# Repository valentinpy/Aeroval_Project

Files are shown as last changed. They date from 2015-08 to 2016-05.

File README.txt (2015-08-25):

AEROVAL
Auteur: Valentin Py  - valentin.py@gmail.com
Date: 22.08.15

Ce projet est le développement d'un PCB ainsi que sa programmation.
Ce PCB est prévu pour le contrôle d'un quadri/octocoptère, mais est aussi utilisable pour un avion ou une voiture.
Pour plus de détails: voir le fichier "functionnalities.txt, ci-joint)

Matériel:
Un PCB de prototype a été développé et produit à 3 exemplaires. "Aeroval-v2-PCB1-proto1.pcbdoc" (gerber utilisés fournis)
Ce PCB fonctionne pour la plupart des fonctions prévues, mais il y aurait quelques améliorations /résolution de problèmes à effectuer:
	- connecteur micro-SD: à retourner de 180°, il n'est actuellement pas possible d'insérer une carte uSD.
	- transistors T1, T2, T3, T4: la numérotation du footprint est fausse, il faut corriger, sinon le transistor sera soudé "à l'envers"
	- Le solder mask est à modifier sous U4, afin de ne pas avoir de résine sous le pad thermique. (bien que ça fonctionne quand même dans l'état actuel)
	
La BOM est fournie et les supplier links sont remplis (pour la plupart) sur Altium.

Logiciel:
Le développement n'est pas terminé, il y a encore pas mal de travail à faire, mais les modules et les interfaces sont déjà programmés pour la plupart.

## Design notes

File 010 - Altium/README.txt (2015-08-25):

NE MARCHE PAS:
Positionnement uSD (retourner de 180°)
T1, T2, T3, T4: numéro des pins croisés (modifier footprint)
Pad thermique U4: enlever masque sous le step down (U4)

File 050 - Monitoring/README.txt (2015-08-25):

AEROVAL - Monitoring
Auteur: Valentin Py, avec une base de Lucas Wagner 
Date: 22.08.15

Télémétrie basique pour le projet Aéroval.
Programme non terminé, mais fonctionne déjà (du moins, en partie)

Fonctionnement: Brancher la carte Aeroval avec le cable USB sur l'ordinateur et choisir le port COM virtuel correspondant dans l'onglet connexion de ce VI.

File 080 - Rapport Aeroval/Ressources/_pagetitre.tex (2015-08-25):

\begin{titlepage}
%marge du haut et grande marge sur la page
%\headsep          = -10.mm
%\enlargethispage{5cm}

\begin{center} 
\hspace{12.45cm}
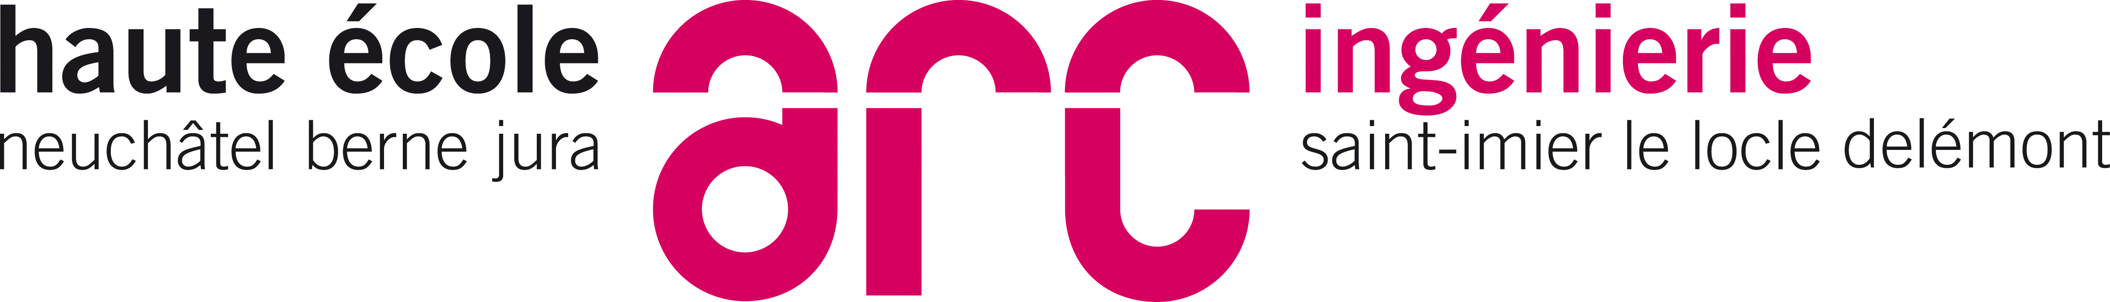
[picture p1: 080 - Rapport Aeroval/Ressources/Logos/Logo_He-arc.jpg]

\end{center}
\vspace{5cm}
% cette commande insert un espace de proportion 1 (par rapport au autre espace insert dans la mÍme apge)
% 1/3 espace, puis ligne
\noindent \rule{\linewidth}{1mm}
\begin{center}
\medskip
{\Huge \nomtitre}\\
\bigskip

\begin{minipage}{0.75 \textwidth}
\begin{center}
{\Large \sousTitre}\\
\end{center}
\end{minipage}~\\

\vspace{0.6cm}
\rule{1cm}{0.3mm}\\
\vspace{0.5cm}

\large \auteurs\\
\medskip
\dateCreation

% ligne, puis 1/3 espace
\noindent \rule{\linewidth}{1mm}
\vspace{3cm}

% Le complement d'information

%les logos des entreprises

\begin{center}

  \small \ecole \\
  %\small Ecole d'IngÈnieurs d'Yverdon-les-Bains \\
  \small \depart
  
\end{center}

\vspace{3.65cm}

%les noms (le "&" sÈpart les colonnes)
\small
{
\begin{tabular}{l@{: }l}
Dernière mise à jour &\today\\
\end{tabular} }

\end{center} 
\end{titlepage}

\newpage

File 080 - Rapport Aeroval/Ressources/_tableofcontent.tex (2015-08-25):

% table des matieres
\pagenumbering{Roman}	
\setcounter{page}{1} % on commence la numération a 1 sur cette page en notation romain
\setcounter{secnumdepth}{5}% profondeur de la table des matieres.
\setcounter{tocdepth}{2} 
\tableofcontents
\setlength{\parindent}{0 cm}% supprime les tabulations à chaque nouveau paragraphe
\newpage
\pagenumbering{arabic} % notation arabe

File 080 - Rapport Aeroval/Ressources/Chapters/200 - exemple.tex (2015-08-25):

% Chapter Template

\chapter{Nom du chaptitre} % Main chapter title

\label{Chapitre 2} % Change X to a consecutive number; for referencing this chapter elsewhere, use \ref{ChapterX}

\lhead{ \emph{Nom du chaptitre}} % Change X to a consecutive number; this is for the header on each page - perhaps a shortened title

Introduction chapitre

%----------------------------------------------------------------------------------------
%	SECTION 1
%----------------------------------------------------------------------------------------
\section{Nom de la section}

Texte section.
%-----------------------------------
%	SUBSECTION
%-----------------------------------
\subsection{Titre sous section}
Texte sous section
\begin{lstlisting}[frame=single,style=C]  % Start your code-block

int main()
{
	printf("exemple en C\n");
	return 0;
}
\end{lstlisting}

Exemple de texte.

\lstinputlisting[frame=single,style=C, title=main.c]{Ressources/Code_Source/main.c}
%\lstinputlisting[language=Python, firstline=37, lastline=45]{source_filename.py}

Texte
\rem{Ceci est une remarque}

\tmpnew{tmp new: A faire!}

\begin{lstlisting}[frame=single,style=Console]
$ Texte console
\end{lstlisting}
\pagebreak Apès un saut de page.

\begin{center} 
\hspace{12.45cm}
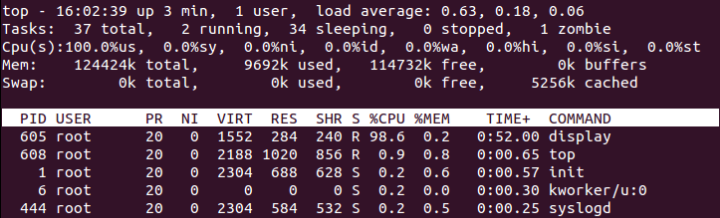
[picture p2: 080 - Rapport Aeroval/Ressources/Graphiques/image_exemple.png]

\end{center}
\vspace{1cm}

Texte

Liste
\begin{enumerate}
\item Premier
\item Deuxième
\item Dernier
\end{enumerate}

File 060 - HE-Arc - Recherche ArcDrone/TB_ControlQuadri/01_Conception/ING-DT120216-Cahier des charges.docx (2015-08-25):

Département de Génie Electrique Travail 12GEL-TB205

Travail de semestre et de Bachelor pour : Favre-Bulle Matthieu

## Système de contrôle de vol pour quadricoptère

### Introduction

La HE-Arc veut développer un quadricoptère comme démonstrateur de son savoir faire dans de nombreux domaines : construction légère en matériaux composite, électronique de contrôle embarquée, régulation automatique, traitement image, communication, gestion de l’énergie embarquée, génération de l’énergie embarquée etc…

### But du projet

Ce projet consiste à développer le système embarqué de contrôle de vol du quadricoptère. Ce système devra pouvoir s’interfacer soit sur les signaux en provenance d’un récepteur d’une télécommande du marché soit, à moyen terme d’un système de gestion de vol automatique embarqué via un bus à définir. Son rôle sera de maintenir le quadricoptère en vol stationaire et de lui faire faire les déplacements demandés par le système de commande supérieur : télécommande ou ultérieurement un système de gestion de vol embarqué. Il devra donc acquérir au moyen des différents capteurs les paramètres de vol du quadricoptère, afin d’être capable de donner des ordres de vitesse aux drivers des 4 moteurs brushless de l’appareil.

### Cahier des charges

Le projet consiste donc à :

1. Développer une carte électronique comportant un microcontrôleur ayant les fonctionnalités suivantes :
- Implémentation et acquisition d’un accéléromètre 3 axes (au centre de la carte)
- Implémentation et acquisition d’un gyroscope 3 axes (au centre de la carte)
- Implémentation et acquisition d’un magnétomètre 3 axes (au centre de la carte)
- Implémentation et acquisition d’un capteur de pression
- Interface de communication série vers capteur altimètre à ultrason, protocole à définir.
- Interface de commande de l’électronique des moteurs brushless à l’aide de signaux PWM normalisés dans le monde du modèle réduit.
- Interface avec un récepteur de télécommande du marché
- Prévoir une interface série dans le but d’implémenter un GPS
- Prévoir des connections pour une carte d’extension (Alim, signaux uP, …)
- Interface de communication radio bidirectionnelle (serial to RF), utiliser un module du marché, permettant d’implémenter des fonctions de télémétrie.
- Interface rapide avec une autre carte à processeur (gestion de vol automatique embarqué, interface et protocole à définir).
- Alimentation de la carte via la tension de sortie régulée d’un des contrôleurs brushless. Prévoir un régulateur de tension pour alimenter les composants de la carte.
- Mesure et surveillance de la tension et du courant de l’accu
- Dimensions de la carte : 100 x 100mm
2. Programmer cette carte pour permettre au quadricoptère d’obéir à des ordres en provenance de la télécommande en prenant en compte les mesures des capteurs et de le maintenir en vol stable. Les contraintes du logiciel sont :
- Prévoir une architecture logicielle en 3 couches étudiée durant les cours d’informatique embarquée
- Prévoir un monitoring permettant d’envoyer et recevoir différents paramètres toutes les 20msec via l’interface RF : La trame utilisée pour la communication devra permettre d’ajouter facilement le monitoring d’autres variables et également la réception de valeurs de variables en provenance du sol.
  - 3 axes accélérations
  - 3 axes vitesse angulaire
  - 3 axes magnétomètre
  - Altitude
  - Tension accu
  - Courant de l’accu
  - Valeur PWM envoyées à chaque moteur

Projet microtechnique

Un autre travail de bachelor dans le domaine des microtechniques sera en charge de la conception du quadricoptère. Communiquer avec l’étudiant responsable de ce projet, afin de vous synchroniser sur l’implantation de la carte électronique, la connectique, etc.

Résultat du projet

A la fin du projet, on disposera :

* d’une liste complète décrivant les solutions étudiées
* d’une présentation détaillée de la solution retenue
* de deux cartes électroniques montées et testées
* d’une architecture logicielle (modèle 3 couches) détaillée
* du code source implémenté sur le dispositif
* d’un schéma détaillé avec liste de pièces et prix du dispositif
* d’une documentation détaillée décrivant l’ensemble du dispositif
* d’un mode d’emploi simplifié

Guide du projet

Phase 1 Conception, calculs et études des solutions (capteurs, choix du microcontrôleur, …)

Phase 2 Présentation de la solution envisagée aux responsables du projet (GHU, PAD, MHU, YME)

Phase 3 Développement matériel, recherche des composants, édition du schéma (Altium Designer)

Phase 4 Réalisation du layout de la carte (Altium Designer)

Phase 5 Sous-traitance de la production des circuits imprimés, et commande des composants

Phase 6 Développement du logiciel du microcontrôleur

Phase 6 Montage du premier prototype, programmation, éventuellement dépannage

Phase 7 Mise en service et tests

Phase 8 Correction de problèmes éventuels (mise à jours schéma et layout)

Phase 9 Documentation

Phase 10 Montage de la 2ème carte électronique (éventuellement production d’un nouveau circuit)

N.B : Prendre garde aux délais de livraison des composants, en principe il faut toujours utiliser des composants de stock chez les distributeurs (Digikey, Mouser, Farnell, Distrelec,...).

# Rapport et évaluation

Le travail de diplôme a entre autre pour but d’évaluer les facultés de l’étudiant à aborder, conduire, exécuter et documenter un travail industriel complet. Spécifié par un cahier de charges et décrit dans un mémoire, il est souvent pluridisciplinaire. Les étudiants voudront bien dans les 4 premières semaines du travail, estimer et planifier les tâches à accomplir.

Délais et rapport selon directives ci-jointes.

HE-Arc/YME/février 2012

ING-DT120216-Cahier des charges2/3 YME-dernière mise à jour : 16.02.2012

ING-DT120216-Cahier des charges1/3 YME-dernière mise à jour : 16.02.2012

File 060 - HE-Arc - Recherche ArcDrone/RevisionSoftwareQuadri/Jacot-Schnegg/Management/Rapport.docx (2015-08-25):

Arc-Drone

Description de la solution retenue

Guillaume Jacot & Alexandre Schnegg

26/01/2013

# Introduction

Le présent document a pour but de résumer le travail effectué sur le quadricoptère afin que le prochain intervenant sache ce qui a été fait. On y trouve les explications concernant la correction des bugs des interfaces ainsi que le fonctionnement du monitoring, de l'acquisition de l'orientation et de la régulation du quadricoptère.

# Résumé du débug des interfaces

## I2C

On a codé une nouvelle fonction permettant la lecture de plusieurs bytes d’un coup. On l’a utilisée pour lire la valeur de tous les axes de l’accéléromètre d’un coup. La lecture multiple ne fonctionne pas avec le gyroscope donc on a laissé comme c’était fait.

On a préféré tester si le bus était libre plutôt que de faire une attente active dans tous les cas.

On a corrigé la fonction d’envoi par I2C. Quand on envoie l’adresse du périphérique souhaité sur le bus I2C, on met le dernier bit à 1 ou à 0 en fonction de si on veut lire ou écrire un registre. Dans notre cas, le dernier bit de la donnée était aussi modifié donc la configuration des périphériques I2C (par exemple la vitesse d’acquisition des données) n’était pas celle que nous voulions.

## Magnétomètre

Une fois qu’une valeur avait été lue, toutes les lectures suivantes nous donnaient les mêmes résultats. On a découvert ceci en faisant des tests avec un aimant :

- Si l’aimant était mis avant le démarrage du programme, les valeurs mesurées étaient grandes et ne bougeaient pas quand on retirait l’aimant.
- Si l’aimant n’était pas mis avant le démarrage du programme, les valeurs mesurées étaient beaucoup plus petites, mais ne bougeaient pas quand on mettait l’aimant.

Ceci était dû au bit LOCK du magnétomètre qui se met à ‘1’ quand on lit la 1re valeur et qui empêche donc l’actualisation des mesures. Celui-ci ne se remettait malheureusement jamais à ‘0’ ce qui empêchait la modification des valeurs.

Pour remédier à ce problème, on a également utilisé notre fonction de lecture multiple par I2C pour lire tous les axes d’un coup. Le magnétomètre remet automatiquement le bit LOCK à ‘0’ quand on a lu toutes les valeurs. Des fois, celui-ci ne se remet pas à ‘0’ automatiquement, on renvoie donc le mode d’acquisition (single ou continuous) au magnétomètre pour forcer sa remise à ‘0’.

On a également modifié le gain, car il était au minimum et le champ magnétique terrestre est très faible (environ 0.5 gauss).

## PWM

La largeur des impulsions variait périodiquement. On a mis pas mal de temps à détecter que ceci venait d’une simple erreur de soustraction dans l’interface du timer. A chaque détection de flanc du signal d’entrée, on sauvegarde la valeur du timer. Ensuite, on calcul la différence entre les 2 mesures. Lorsque le 2e flanc (flanc descendant) est détecté après que le timer soit revenu à 0, il faut prendre la valeur maximale du timer moins la différence entre les 2 valeurs mesurées pour avoir un résultat correct. Le code avait été fait pour une valeur maximale du timer de 65535 pourtant le timer est configuré pour compter de 0 à 62’500 seulement donc les mesures étaient faussées.

Une fois ce problème corrigé, on pouvait encore observer des petites variations dans la mesure du duty cycle alors que le signal d’entrée ne variait pas. Ceci était dû à la façon de sauvegarder la valeur du timer à chaque flanc. En effet, on sauve les valeurs dans des variables globales qui sont ensuite lues par une autre fonction (celle qui fait la soustraction entre les deux valeurs).

Lorsqu’une nouvelle impulsion arrivait (détection du flanc montant), on sauvait la première valeur du timer. Le problème se posait dans le cas où l’autre fonction venait lire, avant le flanc descendant, les deux variables. On avait donc la valeur du timer au flanc descendant de l’ancienne impulsion et au flanc montant de la nouvelle impulsion, ce qui nous donne un résultat faussé.

Pour remédier à ce problème, on met la première valeur dans une variable temporaire et à la fin de l’impulsion, on sauve les deux valeurs dans les variables globales (les deux changent donc en même temps et on a toujours les deux valeurs se rapportant à la même impulsion).

Quand on lit un signal venant de la télécommande, celui-ci a une période de 20 ms, mais l’impulsion ne dure qu’entre 1 et 2ms. Ceci nous donne donc un duty cycle entre 0.05 (5%) et 0.1 (10%). La précision des float n’étant pas très bonne, on a préféré travailler directement avec la valeur en UInt16 (qui représente la soustraction des 2 valeurs du timer). On convertit ensuite cette valeur dans une plage allant de 0 (0%) à 1 (100%).

## Attentes actives

Nous avons remplacé toutes les attentes actives par des machines d’états pour gagner en rapidité car rien que le capteur de pression prenait environ 70ms avant de renvoyer une valeur par exemple.

# Monitoring

## Envoi des données

Les données sont envoyées à l'application labview par le bai d'une communication série sans fil sous forme de chaînes de caractères.

La trame a le format suivant:

1. Start
2. Capteur
3. Type de donnée (entier ou flottant)
4. Données
5. Stop

Lorsque le capteur nécessite l'envoi de plusieurs valeurs (par ex: 3 axes pour l'accéléromètre), les données valeurs sont séparées par le caractère '|'.

La génération des trames se fait avec le l'utilitaire generateTrame.h.

## Application labview

### Fonctions

Voici une liste des capteurs dont les valeurs peuvent être lues par l’application Labview :

- Accéléromètre (3 axes)
- Gyroscope (3 axes)
- Magnétomètre (3 axes)
- Pression
- Température
- Altitude (pas encore fonctionnel)
- Tension de la batterie
- Courant consommé
- Orientation du quadricoptère (3 axes, valeurs après filtrage)
- Signaux PWM (commande des 4 moteurs)

Voici à quoi ressemble l’application :

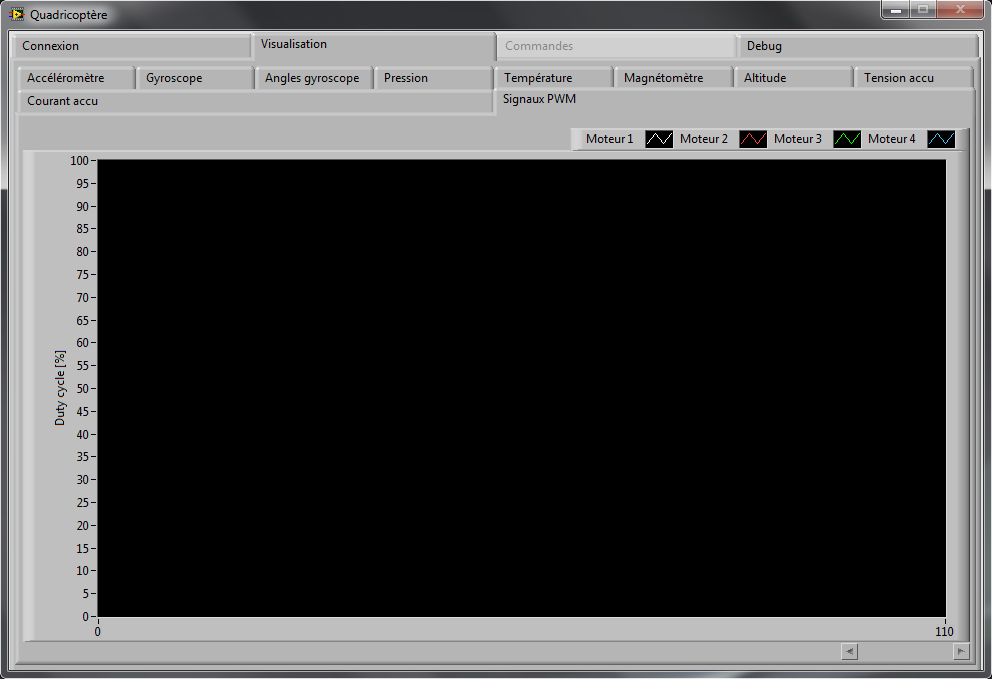
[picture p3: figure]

Fonctions des 4 onglets principaux :

- Connexion : permet de sélectionner sur quel port COM est connecté le récepteur RF, de s’y connecter/déconnecter et de quitter l’application.
- Visualisation : permets de visualiser un graphique par capteur (chaque capteur est sur un onglet séparé) représentant l’évolution des mesures de celui-ci (plusieurs courbes sur le même graphique pour les capteurs avec plusieurs axes ou pour les signaux PWM des 4 moteurs).
- Commandes : permets d’envoyer des commandes au quadricoptère. Cet onglet n’est pas encore fonctionnel.
- Débug : permets de visualiser tout ce qui a été reçu par RS232 et détecter d’éventuelle erreur dans les valeurs envoyées par le quadricoptère. On y voit également la dernière commande reçue ainsi que l’état de l’application.

### Fonctionnement

L’application est basée sur une machine d’état. On passe d’abord par un état d’initialisation, puis par la connexion au RS232 et enfin on va lire les données reçues en boucle. Un état est aussi prévu pour la déconnexion du RS232.

Chaque fois qu’une trame est reçue, l’application va la placer dans une file d’attente. C’est une deuxième boucle qui tourne en parallèle qui va récupérer cette trame, la décoder et ajouter les valeurs qu’elle contient sur le bon graphique.

A chaque fois que la machine d’état passe à l’état « Init », « Connect » ou « Disconnect », une notification est envoyée à une troisième boucle qui tourne en parallèle. Celle-ci s’occupe d’effacer les graphiques et d’activer/désactiver certaines fonctions selon l’état de l’application.

# Acquisition de l'orientation

## Systèmes d'axes des capteurs

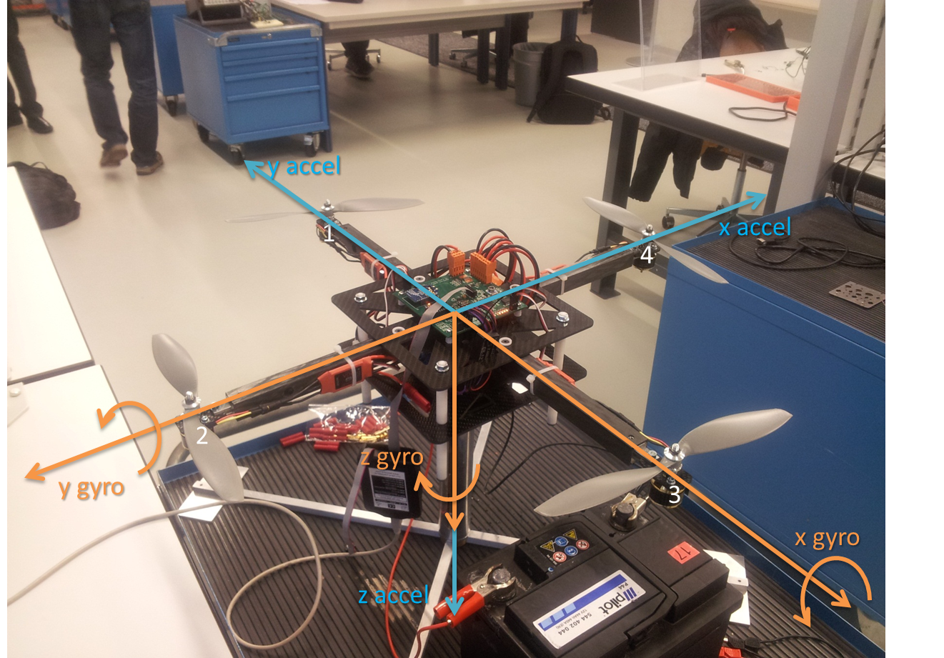
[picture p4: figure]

## Algorithme d'acquisition de l'orientation

Premièrement, les données brutes des capteurs sont transformées en grandeurs physiques (g pour l'accélération et deg/s pour le gyroscope. La dérive du gyroscope est compensée à ce moment-là.

Le vecteur d'accélération est ensuite transformé en angles dans le référentiel du gyroscope. La valeur de ces angles est convertie en degrés.

Dès lors, les valeurs sont filtrées par un filtre du premier ou du second ordre, à choix. Les paramètres du filtre sont réglés dans les définitions du fichier mOrientationProcessing.h. On peut régler la fréquence d'échantillonnage (kDt), le Tau du filtre (kTau) et les coefficients du filtre (kA et kB, respectivement pour le passe-haut (gyroscope) et le passe-bas (accéléromètre)).

# Régulation

Tous les paramètres de la régulation sont réglables dans mRegulation.h.

La régulation fonctionne sur le principe suivant : une puissance constante est appliquée à tous les moteurs. La régulation va calculer la puissance à rajouter ou à enlever. L’erreur est calculée sur les angles xz et yz, qui correspondent aux deux axes d'inclinaison possible; la régulation est calculée pour ces deux angles. La puissance à appliquer au moteur qui sont sur un axe est calculée comme ceci: pour le premier on additionne la puissance calculée par la régulation à l'offset, pour l'autre on la soustrait.

Chaque régulateur (P et I) est implémenté séparément dans une fonction.

Il est nécessaire de régler l'angle maximum que peuvent avoir les angles d'orientation. Lorsque le quadricoptère et sur le support il ne peut s'incliner que de 20°.

# Gestionnaires

La régulation devant être exécutée à un temps régulier précis, le code doit être exécuté dans une interruption. Pour se faire, nous avons créé trois fonctions execute spéciale, gInput_ExecuteInt, gCompute_ExecuteInt, gOutput_ExecuteInt destinées à être appelée dans l'interruption iPit_INTPit1. Les autres fonctions execute sont appelées dans la boucle principale du main.

# Démarrage du quadricoptère

Quand on branche l’alimentation, les drivers moteurs se configurent en fonction du signal PWM qu’ils reçoivent. Ils considèrent que celui-ci représente 0%. Ceci permet d’utiliser correctement toute la plage de puissances. On doit donc envoyer un signal PWM constant représentant le 0% au démarrage du programme avant de pouvoir faire tourner les moteurs à la vitesse souhaitée.

Par mesure de sécurité, le quadricoptère ne démarre pas tout de suite lorsque le programme est démarré. Il faut maintenir les joysticks de la télécommande en position 0 (en bas à gauche) pour que les moteurs démarrent. Sitôt qu’un joystick est relâché, les moteurs s'arrêtent.

# Leds témoin

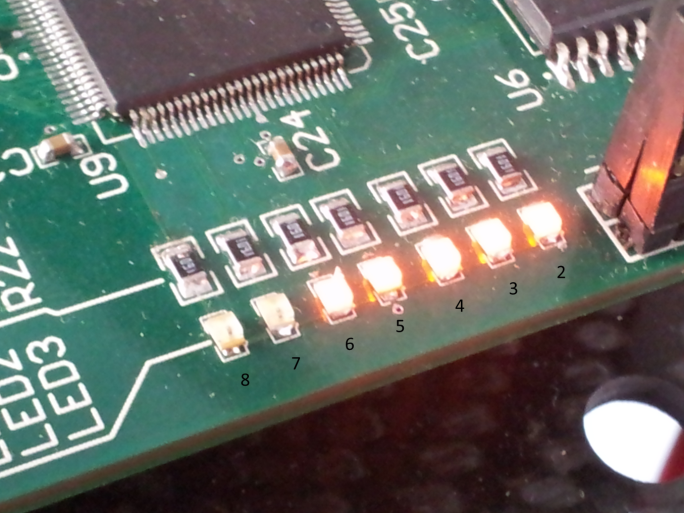
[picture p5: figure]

2. Allumée après le setup des modules
3. Allumée après l'open des modules
4. Allumée après le setup des gestionnaires
5. Clignote à chaque cycle du main
6. Clignote à chaque appel de l'interruption iPit_INTPit1
7. Témoin d'activation des moteurs

Résumé du travail effectué sur le quadricoptère 6/6

Guillaume Jacot INF3iie 28 janvier 2013 Alexandre Schnegg

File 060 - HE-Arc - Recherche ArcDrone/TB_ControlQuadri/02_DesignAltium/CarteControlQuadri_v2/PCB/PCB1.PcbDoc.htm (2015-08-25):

Reporting Options

# File in Previous Format

Date | : | 04.08.2015
Time | : | 11:08:36
Filename | : | C:\Users\valentin.py\Documents\Aeroval\PyValentin\TB_ControlQuadri\02_DesignAltium\CarteControlQuadri_v2\PCB\PCB1.PcbDoc

Version | Warning
Altium Designer update 19 | CAUTION - Air Gap Width attribute was introduced to Polygon Connect Style Rule. Air Gap Width attribute now controls the distance between poured polygon and pads on the same net - this value was previosuly taken from clearance rule while ignoring net subscope leading to sometime unexpected results.
Release 13 | CAUTION - Silkscreen Over Component Pads Rules are converted to Silk To Solder Mask Clearance Rules. Suggest examining rule scopes for accuracy.
Release 14 | CAUTION - The Differential Pairs Routing rule added support for control of the width. Be aware that Width rules pertaining to differential pairs need to be manually moved to the Differential Pairs Routing rule.

This file was generated by an earlier version of the software

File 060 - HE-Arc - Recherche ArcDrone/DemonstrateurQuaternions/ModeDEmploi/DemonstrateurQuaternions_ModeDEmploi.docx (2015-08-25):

# Mode d’emploi démonstrateur quaternions

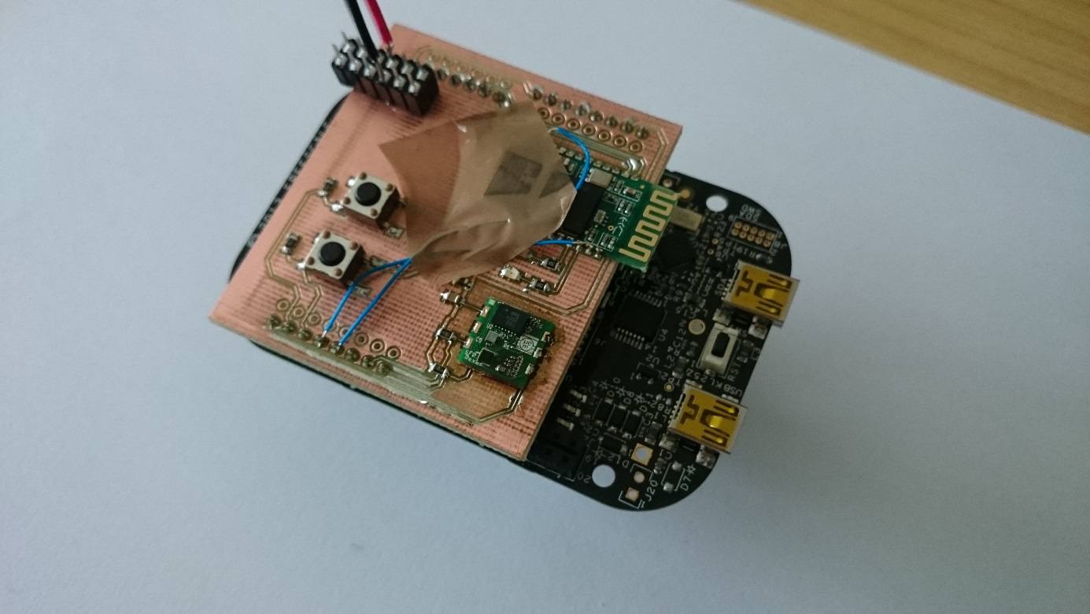
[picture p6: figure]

# Introduction

Le démonstrateur quaternions est une plateforme hardware qui a pour but de lire les valeurs d’un capteur de fusion 9 axes pour ensuite les récupérer avec un ordinateur.

La plateforme utilise un kit de développement de chez freescale, la FRDM-KL25Z. Une carte d’adaptation a été réalisée, elle comporte deux boutons poussoirs, le capteur de fusion ainsi qu’un module bluetooth. Cette carte d’adaptation est branchée sur le kit freescale.

Ultimement, les données seront utilisées pour évaluer les performances de l’algorithme de Madgwick.

# Implentation

Sur l’image ci-dessous, nous pouvons voir :

- Le bluetooth et son antenne (HC-05)
- Le capteur de fusion (EM7180)
- Les boutons poussoirs
- La carte de développement freescale (FRDM- KL25Z)

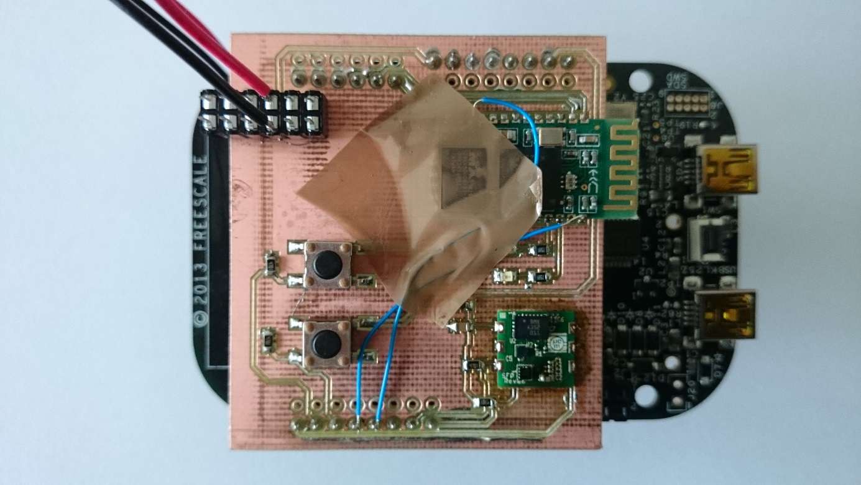
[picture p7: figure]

Ci-dessous, nous voyons :

- La pile d’alimentation 9V
- La fixation de la pile avec des velcros

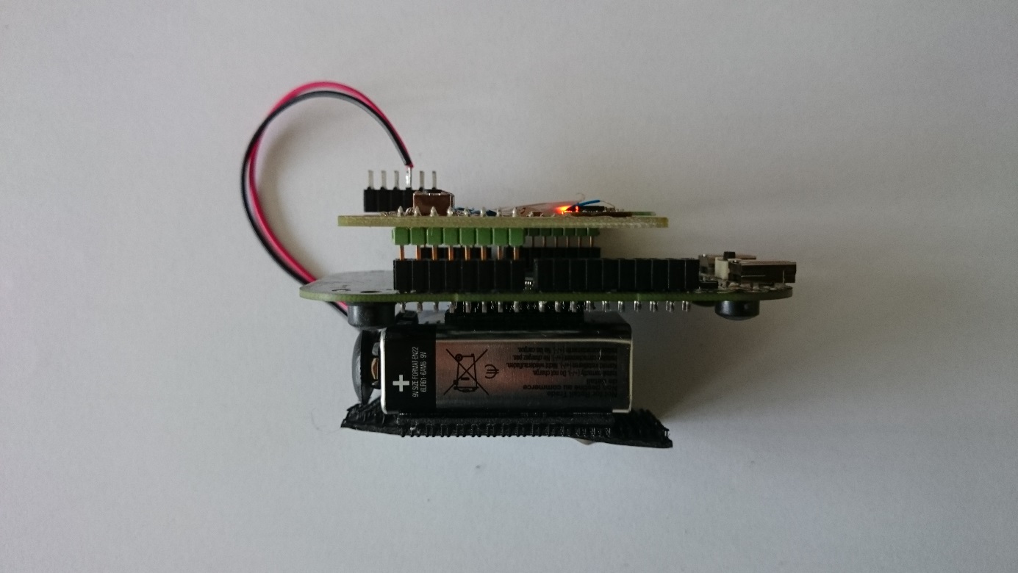
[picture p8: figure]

# Datasets

Des datasets ont été faits.

La fréquence de la mesure est de 100Hz.

Pour ce faire, nous avons fixé le démonstrateur sur une chaussure. Un velcro est passé entre les lacets.

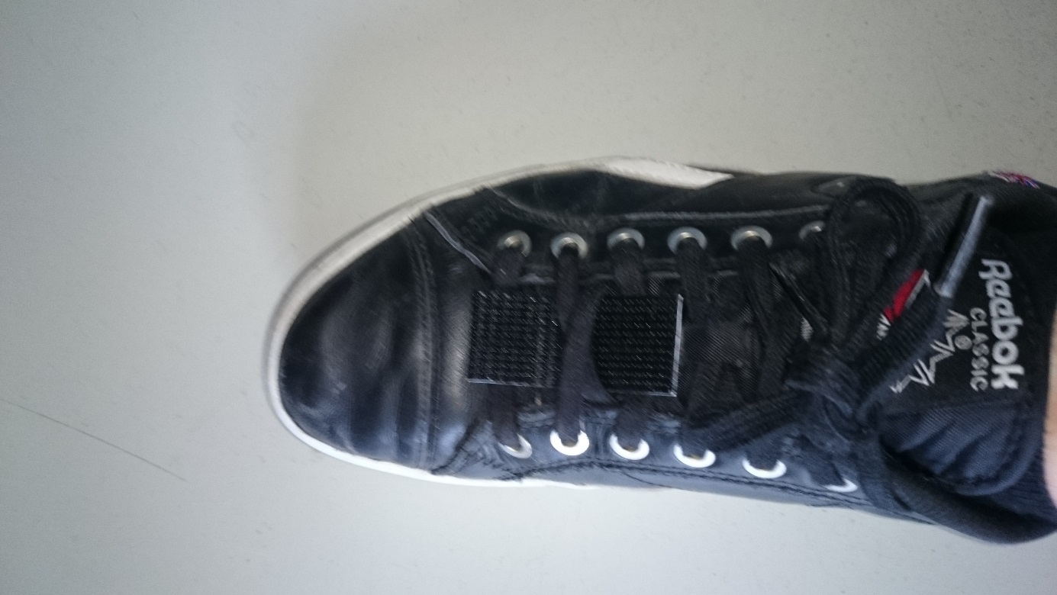
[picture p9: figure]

Des élastiques sont utilisés pour stabiliser la plateforme le plus possible et ainsi éviter le bruit durant la mesure.

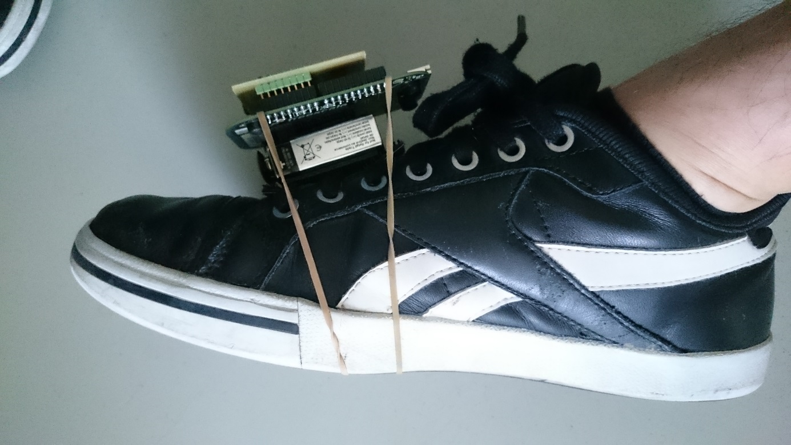
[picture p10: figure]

# Connexion du bluetooth et récupération des données

Les données du capteur de fusion sont transférer vers un ordinateur grâce à un module bluetooth. Elles sont ensuite récupérées dans un terminal (TeraTerm).

Les caractéristiques de transmission sont les suivantes :

- Baudrate : 460900
- Stop bit : 1
- Parity : none

Pour réaliser le transfert de données, il faut :

1) Mettre en marche le bluetooth de l’ordinateur
2) Connecter le module bluetooth HC-05 (password : 1234)
3) Ouvrir les paramètres du bluetooth de l’ordinateur et créer un portcom
4) Ouvrir un terminal et se connecter sur le portcom correspondant avec les bons réglages de communication

Quand la connexion n’est pas effectuée, la led TODO de la carte clignotte vide.

Lorsque la connexion est établie, la led TODO est allumée et la led TODO clignotte deux fois toute les secondes. Attention, si Teraterm n’a pas ouvert de connexions sur le portcom, les leds ne passent pas en état connecté…

# Enclencher et déclencher la mesure

Le bouton poussoir TODO permet d’enclencher et de déclencher l’envoi de données via bluetooth.

Une led bleue sur le kit de développement FRDM- KL25Z s’allume lorsque les données sont en train d’être envoyées.

# Conclusion

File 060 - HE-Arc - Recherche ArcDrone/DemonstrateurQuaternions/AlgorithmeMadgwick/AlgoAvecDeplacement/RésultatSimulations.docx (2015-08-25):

Ligne droite, seulement gyroscope

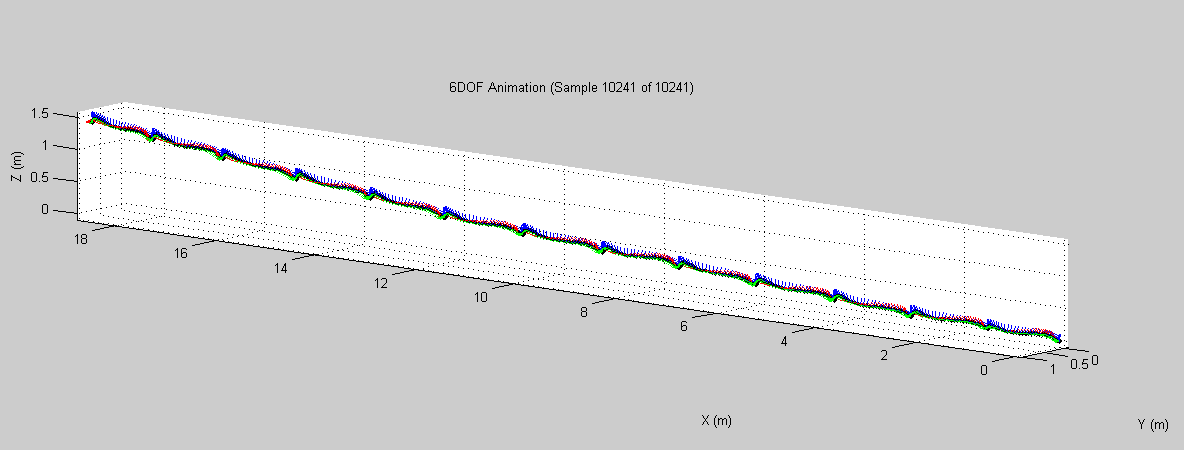
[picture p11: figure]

Ligne droite, UpdateIMU_LS

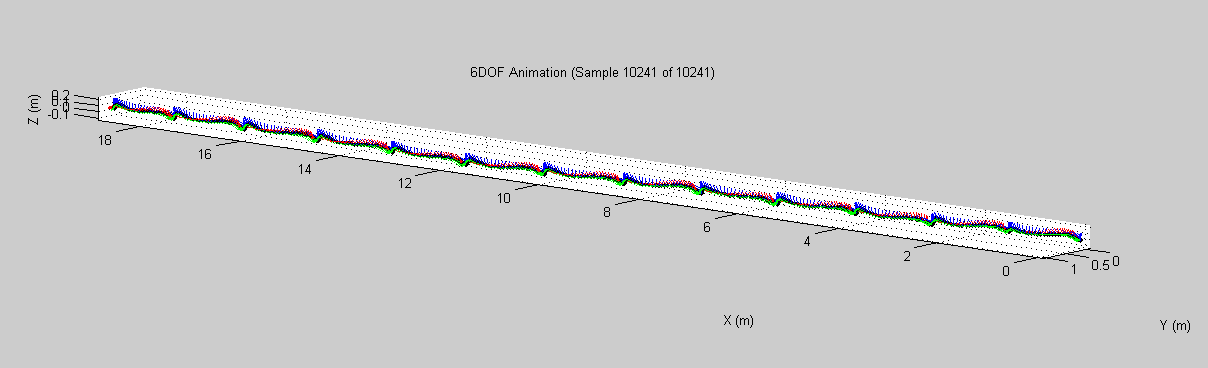
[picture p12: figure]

Ligne droite, UpdateIMU_PID

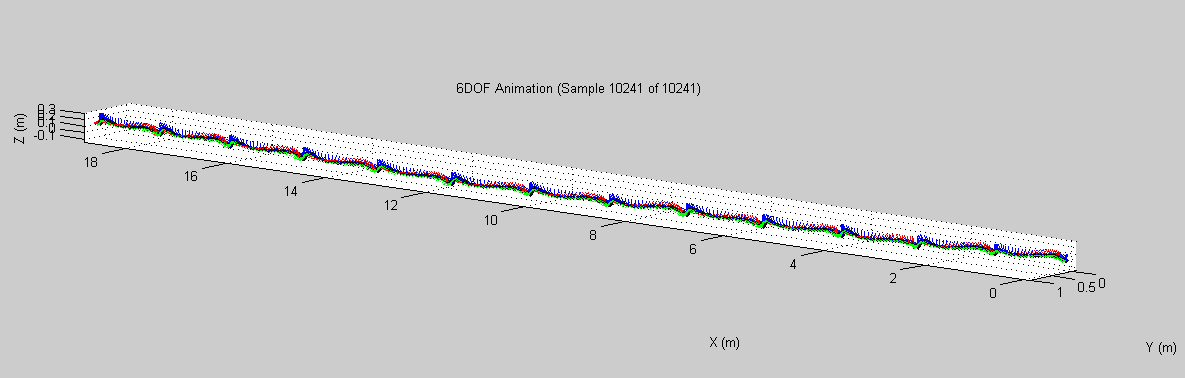
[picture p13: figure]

Corridor et escalier, seulement gyroscope

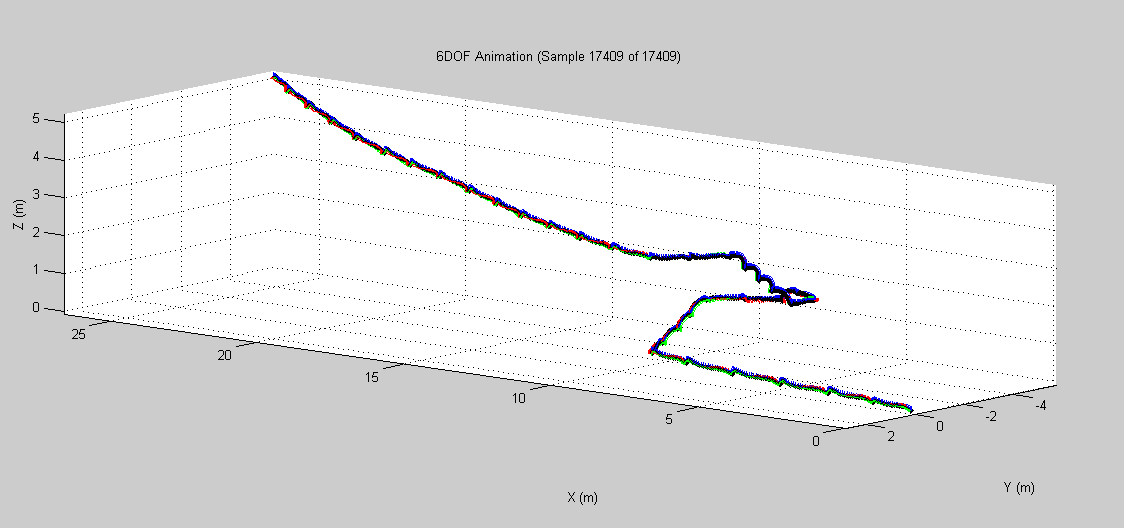
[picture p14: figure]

Corridor et escalier, UpdateIMU_LS

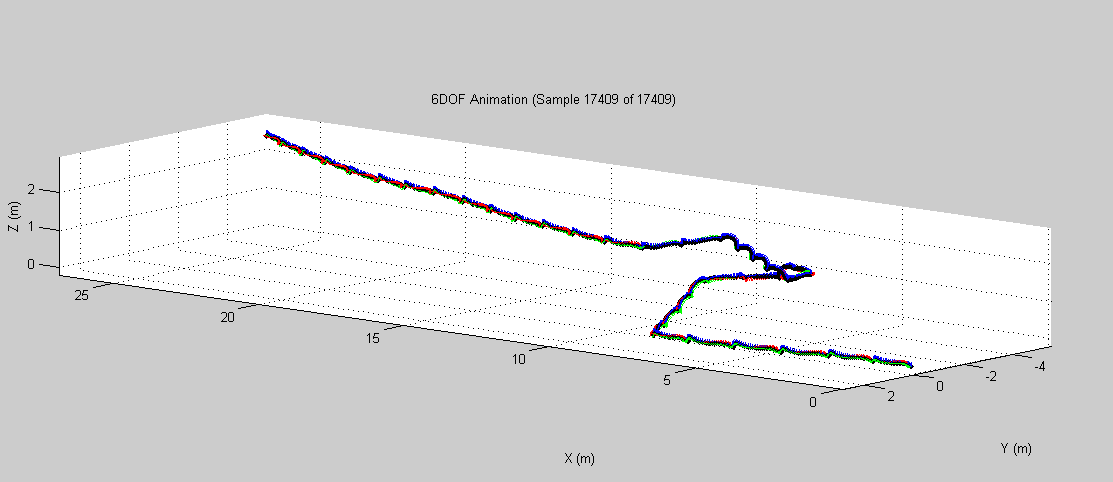
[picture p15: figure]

Corridor et escalier, UpdateIMU_PID

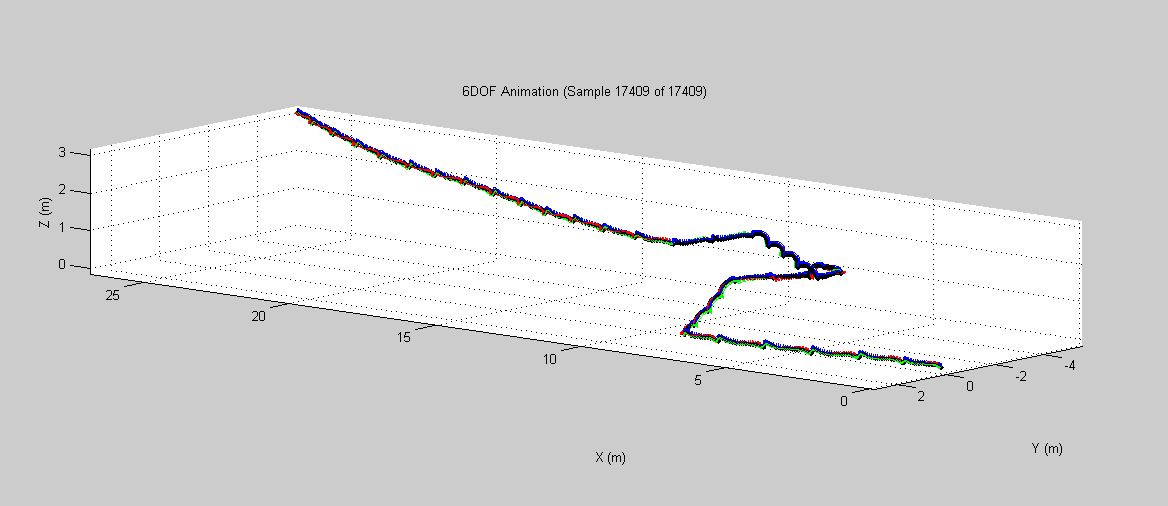
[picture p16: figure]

Escalier, gyroscope uniquement

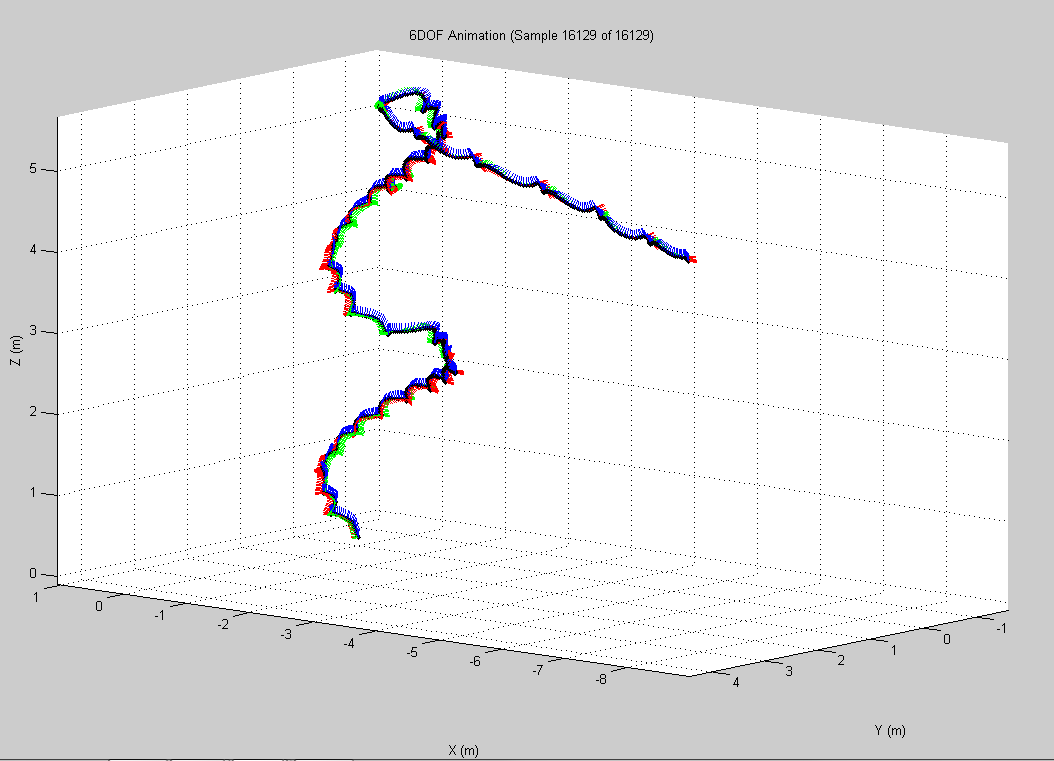
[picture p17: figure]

Escalier, Least squares

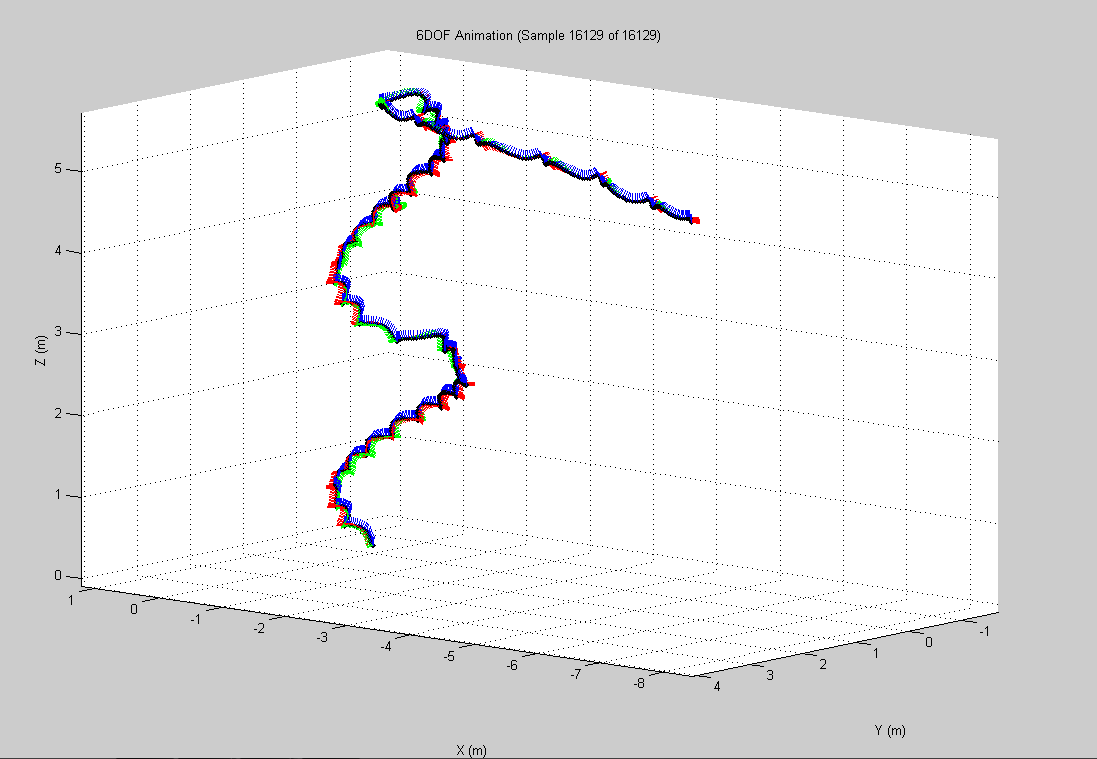
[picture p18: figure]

Escalier, PID

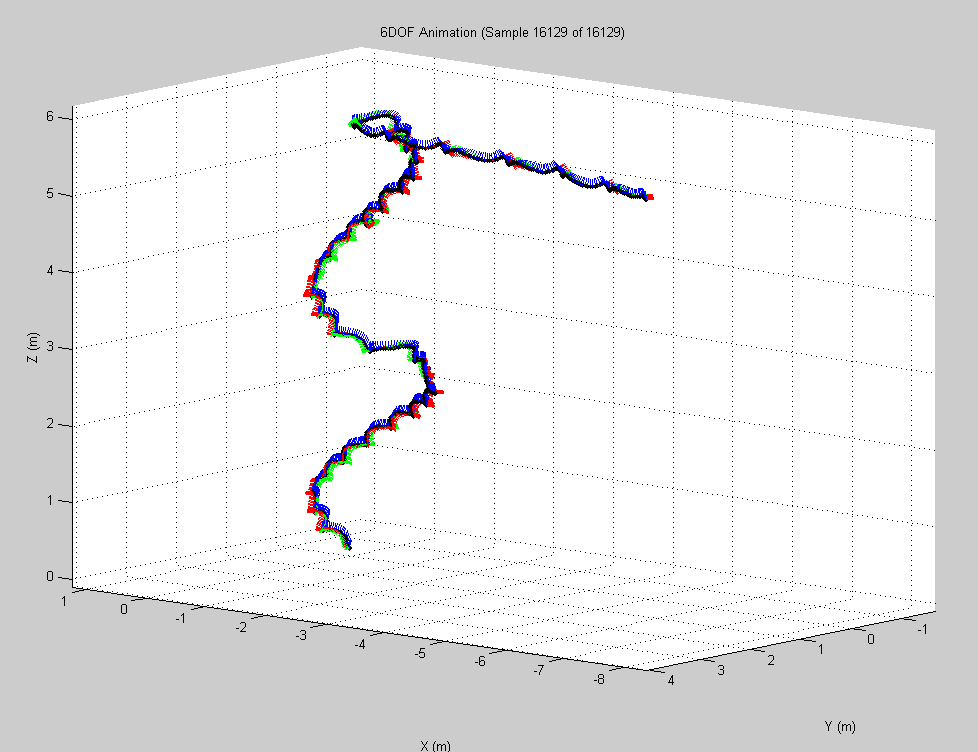
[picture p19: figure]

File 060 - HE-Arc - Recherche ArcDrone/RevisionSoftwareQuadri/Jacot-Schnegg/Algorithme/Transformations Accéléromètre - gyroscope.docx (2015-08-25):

Transformations Accéléromètre - gyroscope

La première difficulté lorsqu’on couple un accéléromètre et un gyroscope, c’est qu’ils ne travaillent pas dans le même système de coordonnées.

Un accéléromètre va donner les trois composantes cartésiennes de l’accélération :

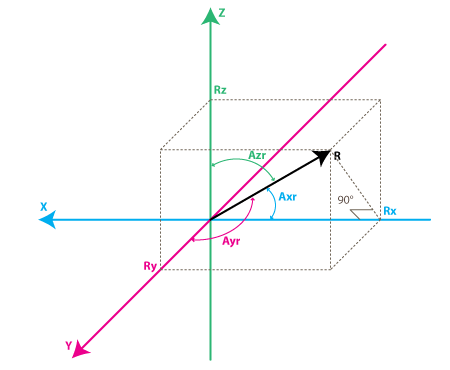
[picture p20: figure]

Source : http://www.starlino.com/imu_guide.html

Les angles Axr, Ayr et Azr sont tendus dans l’espace entre chaque axe et le vecteur Racc.

Un gyroscope va donner la dérivée de trois angles définis différemment : Axz, Axy et Ayz sont les angles définis par les projections du vecteur R sur les trois plans xOz, xOy et yOz.

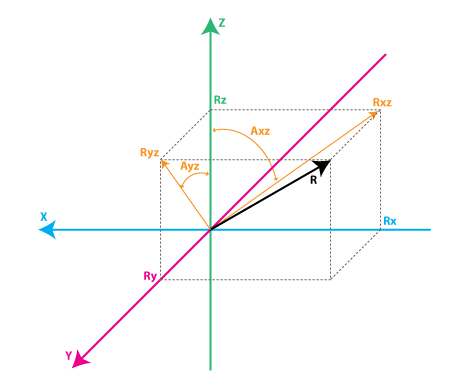
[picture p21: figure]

Source : http://www.starlino.com/imu_guide.html

Le « Système accéléromètre » est intéressant parce que tout est dans un seul vecteur.

Le « Système gyroscope » est intéressant car les axes décrivent exactement les données de navigation « roulis, tangage et lacet » (en anglais : roll, pitch and yaw).

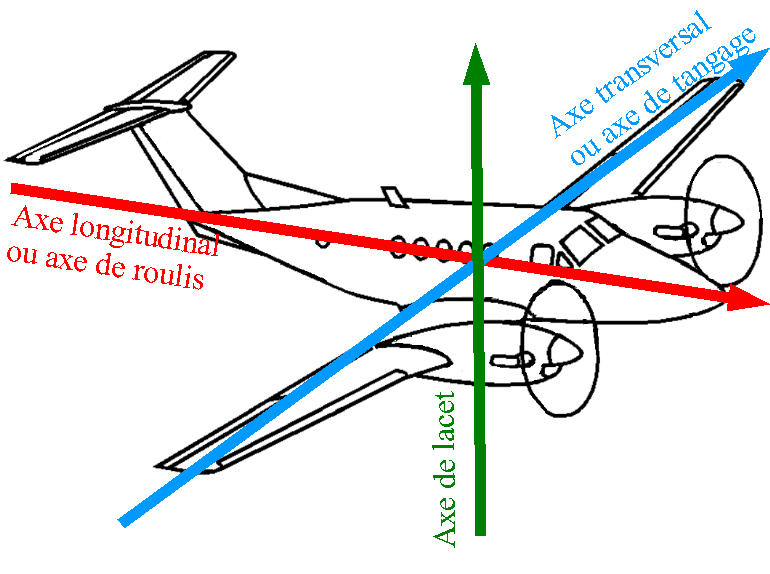
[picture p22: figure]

Source : Wikipedia

# Transformation Système Accéléromètre → Système Gyroscope

Donnée de départ :

Données d’arrivée : Angles Axz, Axy et Ayz

On a :

La fonction « angle » est un arctan généralisé dans les quatre quadrants du plan.

# Transformation Système Accéléromètre → Système Gyroscope

Donnée de départ : Angles Axz, Axy et Ayz (note : deux angles sont en principe suffisants)

Données d’arrivée :

Démarche en pseudo-code:

If Axz = π/2 ou -π/2 %Peut-être faudra-t-il ajouter une tolérance, par ex « If abs(abs(Axz)-π/2)<tol »

Rx = 0; %Signal entièrement dans le plan yOz

Ry = cos(Ayz) ;

Rz = cos(Ayz) ;

Else

if -π/2 < x < π/2

Rx = 1; %Quadrants 1 et 4 du plan xOz, donc x > 0

Else

Rx = -1 ; %Quadrants 2 et 3 du plan xOz, donc x > 0

End if

Rz = tan(Axz);

If Axy = π/2 ou -π/2 %Ici aussi il faut voir s’il y a une tolerance à appliquer

Ry = 0;

Else

Ry = tan(Axy)

End if

%Ici on pourrait tester la cohérence Ayz = angle(Ry,Rz)

%On normalise pour obtenir un vecteur unitaire

Rx = Rx/sqrt(Rx²+Ry²+Rz²); Ry = Ry/sqrt(Rx²+Ry²+Rz²); Rz = Rz/sqrt(Rx²+Ry²+Rz²);

End if

La solution donnée par http://www.starlino.com/imu_guide.html semble bien compliquée. En n’utilisant que Axz et Ayz on trouve :

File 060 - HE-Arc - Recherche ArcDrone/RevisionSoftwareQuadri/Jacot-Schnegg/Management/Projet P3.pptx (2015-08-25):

## Projet P3 Arc-Drone

Alexandre Schnegg & Guillaume Jacot

Alexandre Schnegg & Guillaume Jacot Arc Drone

## Sommaire

- Introduction
- Debug des interfaces
- Hardware
- Acquisition de l’orientation
- Régulation
- Commande des moteurs
- Monitoring
- État de fonctionnement
- Améliorations
- Conclusion

## Introduction/buts

- Prise en main du quadricoptère
- Debug des interfaces existantes
- Assembler le quadricoptère
- Maintenir le quadricoptère en vol stable
- Réaliser un monitoring du quadricoptère

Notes: Introduire le contexte et expliquer les buts du projet.

## Débug des interfaces

- Réécriture des fonctions de communication I2C
  - Lecture de plusieurs bytes à la fois sur l’accéléromètre
  - Mais pas sur le gyroscope
- Suppression des attentes actives
  - Test si le bus est libre dans le cas de l’I2C
  - Machine d’état dans les autres cas
- Correction de l’envoi par I2C
  - Donnée modifiée

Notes: On a codé une nouvelle fonction permettant la lecture de plusieurs bytes d’un coup. On l’a utilisée pour lire la valeur de tous les axes de l’accéléromètre d’un coup. La lecture multiple ne fonctionne pas avec le gyroscope donc on a laissé comme c’était fait.

On a préféré tester si le bus était libre plutôt que de faire une attente active dans tous les cas.
Nous avons remplacé toutes les attentes actives par des machines d’états pour gagner en rapidité car rien que le capteur de pression prenait environ 70ms avant de renvoyer une valeur par exemple.


On a corrigé la fonction d’envoi par I2C. Quand on envoie l’adresse du périphérique souhaité sur le bus I2C, on met le dernier bit à 1 ou à 0 en fonction de si on veut lire ou écrire un registre. Dans notre cas, le dernier bit de la donnée était aussi modifié donc la configuration des périphériques I2C (par exemple la vitesse d’acquisition des données) n’était pas celle que nous voulions.

## Le cas du magnétomètre

- Lisait toujours la même valeur (la première)
  - Bit LOCK
- Changement du gain
  - Lecture du champ magnétique terrestre

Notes: Une fois qu’une valeur avait été lue, toutes les lectures suivantes nous donnaient les mêmes résultats. On a découvert ceci en faisant des tests avec un aimant :
- Si l’aimant était mis avant le démarrage du programme, les valeurs mesurées étaient grandes et ne bougeaient pas quand on retirait l’aimant.
- Si l’aimant n’était pas mis avant le démarrage du programme, les valeurs mesurées étaient beaucoup plus petites, mais ne bougeaient pas quand on mettait l’aimant.
Ceci était dû au bit LOCK du magnétomètre qui se met à ‘1’ quand on lit la 1re valeur et qui empêche donc l’actualisation des mesures. Celui-ci ne se remettait malheureusement jamais à ‘0’ ce qui empêchait la modification des valeurs.

Pour remédier à ce problème, on a également utilisé notre fonction de lecture multiple par I2C pour lire tous les axes d’un coup. Le magnétomètre remet automatiquement le bit LOCK à ‘0’ quand on a lu toutes les valeurs. Des fois, celui-ci ne se remet pas à ‘0’ automatiquement, on renvoie donc le mode d’acquisition (single ou continuous) au magnétomètre pour forcer sa remise à ‘0’.

On a également modifié le gain, car il était au minimum et le champ magnétique terrestre est très faible (environ 0.5 gauss).

## Instabilité PWM

- La largeur d’impulsion mesurée variait périodiquement
- Variation de la puissance par intermittence
  - Erreur de précision des float
  - Variables globales

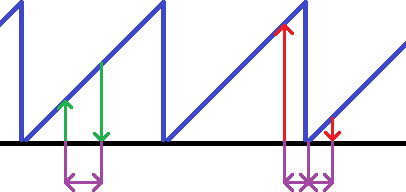
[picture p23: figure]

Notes: La largeur des impulsions variait périodiquement. On a mis pas mal de temps à détecter que ceci venait d’une simple erreur de soustraction dans l’interface du timer. A chaque détection de flanc du signal d’entrée, on sauvegarde la valeur du timer. Ensuite, on calcul la différence entre les 2 mesures. Lorsque le 2e flanc (flanc descendant) est détecté après que le timer soit revenu à 0, il faut prendre la valeur maximale du timer moins la différence entre les 2 valeurs mesurées pour avoir un résultat correct. Le code avait été fait pour une valeur maximale du timer de 65535 pourtant le timer est configuré pour compter de 0 à 62’500 seulement donc les mesures étaient faussées.

Une fois ce problème corrigé, on pouvait encore observer des petites variations dans la mesure du duty cycle alors que le signal d’entrée ne variait pas. Ceci était dû à la façon de sauvegarder la valeur du timer à chaque flanc. En effet, on sauve les valeurs dans des variables globales qui sont ensuite lues par une autre fonction (celle qui fait la soustraction entre les deux valeurs).

## Hardware

- Un moteur consomme 15 A au maximum
- La résistance shunt est dimensionnée pour 50 A
  - Ne pas mettre la puissance des moteurs au max
- Alimentation par batterie de voiture pour les essais
  - L’autonomie de la batterie Li-Po est faible

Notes: Moteur à 70% = environ 43A

## Axes des capteurs

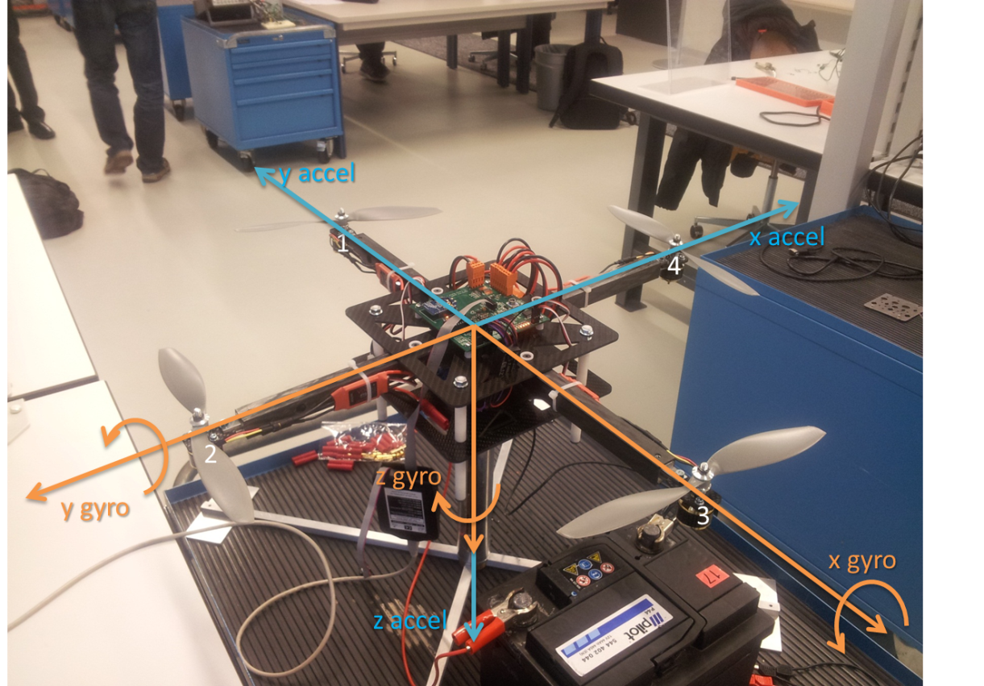
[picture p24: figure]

## Données des capteurs

- Magnétomètre
  - ±1.3 Gauss (champ magnétique terrestre = 0.5 Gauss)
- Accéléromètre
  - ±2 g
- Gyroscope
  - ±250 °/s

## Acquisition de l’orientation

- Acquisition des données brutes
- Transformation du vecteur d’accélération dans le référentiel du gyroscope
- Filtrage des données avec un filtre complémentaire du 1er ordre
θ(n)=a∗[θ(n−1)+θ(n)∗T_s ]+b∗θ(n)
Avec τ=a/(1−a)∗T_s et b=1−a
- Filtre complémentaire du second ordre implémenté

## Régulation

- On choisit une puissance constante pour les moteurs (par ex: 70%)
- On choisit la variation de puissance que la régulation va engendrer (par ex: ±30%)
- On calcule l’erreur pour deux axes (xz et yz)
- Addition / soustraction en fonction du moteur
- Régulateurs PI implémentés
  - I non fonctionnel

## Delay vs Interruption

- En premier lieu la régulation était codée dans la boucle principale du programme
  - Temps de cycle trop long pour assurer un échantillonnage à 10ms
  - Essentiellement dû au monitoring
- Finalement, création de gestionnaires spéciaux appelés depuis une RTI
  - Il est possible de descendre jusqu’à 4ms

## Delay vs Interruption

- Problème d’interruption de la communication I2C avec le magnétomètre
  - Pour corriger, on le lit dans la RTI
- Inversion priorité interruption input capture et RTI

## Commande des moteurs

- Initialisation des drivers moteurs au démarrage
- Au départ, commande des moteurs directement avec la télécommande
- Ensuite, utilisation de la télécommande comme interrupteur

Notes: Quand on branche l’alimentation, les drivers moteurs se configurent en fonction du signal PWM qu’ils reçoivent. Ils considèrent que celui-ci représente 0%. Ceci permet d’utiliser correctement toute la plage de puissances. On doit donc envoyer un signal PWM constant représentant le 0% au démarrage du programme avant de pouvoir faire tourner les moteurs à la vitesse souhaitée.

Par mesure de sécurité, le quadricoptère ne démarre pas tout de suite lorsque le programme est démarré. Il faut maintenir les joysticks de la télécommande en position 0 (en bas à gauche) pour que les moteurs démarrent. Sitôt qu’un joystick est relâché, les moteurs s'arrêtent.

## Monitoring

- Labview
- Permets uniquement la réception de données pour le moment
  - Valeurs en chaîne de caractères
  - Capteurs
    - Accéléromètre
    - Gyroscope
    - Magnétomètre
    - Pression
    - Température
    - Altitude (pas encore fonctionnel)
    - Tension de la batterie
    - Courant consommé
    - Orientation du quadricoptère
    - Signaux PWM

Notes: Le monitoring est fait en Labview.
Pour le moment on peut seulement recevoir des données envoyées depuis le quadricoptère.
Les valeurs sont convertient en chaîne de caractères avant d’être envoyée ce qui n’est pas une très bonne méthode.

## Monitoring


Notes: Image du programme Labview

## État de fonctionnement

- Tous les problèmes détectés dans les interfaces ont été résolus
- L’acquisition de l’orientation fonctionne, mais un ajustement du filtrage est nécessaire
  - La régulation sera plus facile si le bruit est faible
- La régulation a été implémentée, mais le régulateur I n’est pas fonctionnel
  - Essai avec le régulateur P, mais nous n’avons pas encore réussi à stabiliser le quadricoptère
- Monitoring de tous les capteurs fonctionnel

## Comparaison au cahier des charges

- Prise en main du quadricoptère
- Debug des interfaces existantes
- Assembler le quadricoptère
- Maintenir le quadricoptère en vol stable
  - Acquisition orientation
  - Implémentation régulation
  - Vol stable
- Réaliser un monitoring du quadricoptère
  - Monitoring
  - Envoi de commande depuis labview

## Améliorations

- Pour le monitoring, prévoir un envoi des données sous forme binaire
  - L’envoi de chaine de caractère est trop lourd
- Inventer un support qui donne plus de liberté au quadricoptère tout en limitant les risques de casse
- Réglage des gains des régulateurs depuis Labview
- Régulation en logique floue ?

## Conclusion

- Projet intéressant et «fun»
- Les buts du projet ont été atteints ou au moins partiellement
- À faire différemment
  - Envoi des données à Labview
  - On aurait dû directement coder la régulation dans une RTI
  - Coder directement les gestionnaires

## Bonus

## Questions

?

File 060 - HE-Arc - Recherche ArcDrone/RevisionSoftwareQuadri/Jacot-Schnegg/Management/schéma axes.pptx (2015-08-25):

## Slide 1


y accel

1

4

x accel

2

z gyro

y gyro

3

x gyro

z accel

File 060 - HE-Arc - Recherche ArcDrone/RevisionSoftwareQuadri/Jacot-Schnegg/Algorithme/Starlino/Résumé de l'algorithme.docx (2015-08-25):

Résumé de l’algorithme (voir http://www.starlino.com/imu_guide.html)

On veut les 3 coordonnées du vecteur accélération Rest. Pour cela, on a le vecteur de l’accéléromètre Racc, qui n’a pas besoin d’être modifié : ses coordonnées sont directement compatibles. Le problème est que Racc est bien trop bruité et imprécis. On a encore les deux grandeurs du gyroscope RateAxz et RateAyz. Ces deux grandeurs devont être travaillées.

Initialisation :

normalisation de Racc

Fonctionnement :

normalisation de Racc

Gyro : angles des projections

calcul de Rgyro normalisé

Kalman simplifié (5≤w≤20)

normalisation de Rest

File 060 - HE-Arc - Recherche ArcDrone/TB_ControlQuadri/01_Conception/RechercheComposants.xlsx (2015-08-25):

 | Composant | type de communication | Caractéristiques | Référence | Questions
 | MicroControleur |  |  | http://search.digikey.com/ch/fr/products/MK10DN512ZVLL10R/MK10DN512ZVLL10R-ND/2817339
 | accéléromètre 3 axes | SPI | 9 degré of freedom | http://www.mouser.com/stmicrolsm303dlm/
 | gyroscope 3 axes | SPI
 | magnétomètre 3 axes | SPI
 | capteur de pression | SPI | alim+Capteur de l'école | I:\ING\Formation\010-Bachelor\040-TravailBachelor\GEL\12GEL-TB205-ControlQuadri\010-Etudiants\01_Conception\Capteur de pression et de température
 | altimètre Ultrason | Rs232 | alim
 | Interface Commande Moteur | 4xPWM
 | Interface telecomande | 4xTimer | alim | http://www.graupner.de/fr/products/d3601541-a7a0-4f5f-8f0a-a624d262d28f/productcategory.aspx |  | http://fr.wikipedia.org/wiki/H%C3%A9licopt%C3%A8re_radiocommand%C3%A9
 | Interface GPS | Rs232 | alim+io
 | Interface DataTelemetrie | Rs232 | Module 433MHz | http://fr.mouser.com/ProductDetail/Nordic-Semiconductor/nRF905/ http://fr.mouser.com/Search/Refine.aspx?Keyword=MC13201 http://fr.mouser.com/Semiconductors/RF-Semiconductors/RF-Transceiver/_/N-3ri0r | FM, Bluetooth, Zigbee? Module 433MHz
 | Interface Extension | SPI | SPI + alim + io
 | Interface Gestion de vol | SPI | SPI + alim + io
 | Mesure Tension batterie | AD
 | Mesure Courant batterie | AD
 | Affichage (Led ou petit ecran)
 | Telecommande |  |  | http://www.graupner.de/fr/products/1d80881f-8353-4c86-8a6d-2ebefc64e1c1/productcategory.aspx
 | Composant | type de communication | Caractéristiques | Référence | Questions
 | MicroControleur |  | Freescale MK10DN512ZVLL10 | http://search.digikey.com/scripts/dksearch/dksus.dll?vendor=0&keywords=MK10DN512ZVLL10R
 | accéléromètre 3 axes | I2C0 | STM LSM303DLHC | http://fr.mouser.com/ProductDetail/STMicroelectronics/LSM303DLHC/?qs=sGAEpiMZZMtr%2fYvQ9FuPdDRUVbQn7V4k | http://www.digikey.com/product-detail/en/LSM303DLHCTR/497-11918-1-ND/2757636
 | magnétomètre 3 axes | I2C0 | STM LSM303DLHC
 | gyroscope 3 axes | I2C1 | L3G4200D | http://fr.mouser.com/ProductDetail/STMicroelectronics/L3G4200D/?qs=sGAEpiMZZMtlZAfbtrLey%252by4mKX%2fvdEL | http://www.digikey.com/product-search/en/sensors-transducers/gyroscopes/1967243?k=L3G4200D
 | altimètre Ultrason | UART0 | alim
 | Interface Commande Moteur | 4xPWM
 | Interface telecomande | 4xTimer | alim | http://www.graupner.de/fr/products/d3601541-a7a0-4f5f-8f0a-a624d262d28f/productcategory.aspx
 | Interface GPS | UART4 | alim+io |  | Pourquoi met-on la puce GPS sur une carte externe? Pourquoi pas sur la carte gestion de vol ou sur "ma" carte
 | capteur de pression | SPI1 | alim+Capteur de l'école | http://search.digikey.com/scripts/dksearch/dksus.dll?vendor=0&keywords=ms5534
 | Interface DataTelemetrie | SPI2 | MaxStream
 | Interface Extension | UART3 | SPI + alim + io |  | SPI + alim + io
 | Interface Gestion de vol | SPI0 | SPI + alim + io
 | Mesure Tension batterie | AD
 | Mesure Courant batterie | AD
 | Affichage (Led ou petit ecran)
G2 | Crystal oscillator 4 MHz |  |  | http://search.digikey.com/us/en/products/ECS-40-20-5PX-TR/XC1238CT-ND/827702
C1 | Cx |  |  | http://search.digikey.com/us/en/products/GQM2195C1H200JB01D/490-3607-1-ND/789607
C2 | Cy |  |  | http://search.digikey.com/us/en/products/GQM2195C1H200JB01D/490-3607-1-ND/789607
-- | Rf |  | intégrée dans le uC??? (page550)
G1 | Crystal oscillator 32 kHz |  | page 561 | http://search.digikey.com/us/en/products/ABS25-32.000KHZ-T/535-10242-1-ND/2218055
 | DCDC 3.3V |  |  | http://search.digikey.com/us/en/products/MAX763ACSA%2B/MAX763ACSA%2B-ND/1513243
Regulateur de tension
 | 3.3v |  |  | http://search.digikey.com/us/en/products/AP1117T33L-U/AP1117T33L-UDI-ND/1301178
driver mosfet
 | alegro a2982
 | mic4426 |  |  | http://search.digikey.com/us/en/products/MIC4426YM%20TR/576-1202-1-ND/771868
Mesure courant | http://www.maxim-ic.com/app-notes/index.mvp/id/746
CapacitorDigikey | http://www.digikey.com/product-search/en/capacitors/ceramic/131083

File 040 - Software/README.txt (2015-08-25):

Software Aeroval

Auteurs: Valentin Py, avec du code provenant aussi de Serge Monnerat et Timothée Fivaz
Etat: 22.08.15 Interfaces et Modules prêts pour la plupart, gestionnaires créés, à compléter.

IDE: Kinetis Design Studio V3.0
(Pour utiliser Codewarrior, créer un nouveau projet, copier les sources et modifier la table des vecteurs d'interruption
Emplacement sur KDS: Project_Settings/Startup_Code/startup_MK64F12.S

Interfaces et Modules prêts pour la plupart, gestionnaires créés, à compléter.

Les mises à jour effectuées par Valentin Py sont disponibles ici:
https://github.com/valentinpy/Aeroval_Software
ou par e-mail: valentin.py@gmail.com

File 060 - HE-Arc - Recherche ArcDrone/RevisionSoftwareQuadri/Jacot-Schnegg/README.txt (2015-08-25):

Algorithme:
Contient les documents concerant le filtre complémentaire.

Management:
Contient le journal de travail au format OneNote et pdf, le planning,la présentation, le schéma des axes des capteurs, et le rapport.

Software
Contient l'application Labview et le workspace CodeWarrior.
Le fichier quadrip3_r42.gz permet de restaurer le repository SVN.

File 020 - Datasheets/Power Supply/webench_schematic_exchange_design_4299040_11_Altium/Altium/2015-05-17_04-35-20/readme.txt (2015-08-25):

**********************************************************
*******************  PCB Instructions  *******************
**********************************************************

To import your new BOARD into Altium:

1. Start the Altium program.
2. From the menu select "File"->"Open".
3. Select the file named in the path above ending with ".pcbdoc"
   and "Open" the file.
4. Planes will need to be repoured to update the Copper Pour Polygons
	a. Once your board is loaded, select the Tools menu from the
	   top Menu Bar
	b. Scroll to the Polygon Pours item on the Tools Menu.
	c. The Polygon Pours item should expand to show more options
	d. Select Repour All Polygons, this will repour all of the
	   polygons.
5. Your board should be viewable within Altium now.

For additional information, please visit this site:
http://www.accelerated-designs.com/help/Altium_BrdSch_import.html

**********************************************************
*******************  LIB Instructions  *******************
**********************************************************

To import your new LIBRARY PARTS into Altium follow these steps:

1. After running the Ultra Librarian export for the first time,
   you will need to copy the following files into an area where
   they can be accessed for all future translations.  They are script
   files that Altium will need to be able to find.
	a. UL_Form.dfm
	b. UL_Form.pas
	c. UL_Import.pas
	d. UL_Import.prjScr
2. The above script file will need to be run from within Altium.
   This can be done by going to File, Open and selecting the
   UL_Import.PrjScr file stored above.
3. Select the "DXP" dropdown menu in the top-left corner runfrom
   the drop down menu and select "Run Script". Select "UL_Form.pas"
   and click "OK"
4. When the script is run, it will ask you for the file name of the
   Ultra Librarian file to run. Click "File...", select the latest file
   produced with a date code (for instance 2010-02-17_23-12-34.txt), and
   click "Start Import".
5. The script will open a new Integraged Library project and import
   the Ultra Librarian data into it.  When complete a message box
   will pop up saying that import is done.

For additional information, please visit this site:
http://www.accelerated-designs.com/help/Altium_import.html

For a video tutorial, please visit:
http://youtu.be/pih50yx9HYU

**********************************************************
**********************************************************
**********************************************************

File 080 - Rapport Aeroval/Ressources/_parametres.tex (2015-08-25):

% classe du document
\documentclass[11pt,a4paper]{report}

% packages
\usepackage[T1]{fontenc}
\usepackage{mathtools}

\usepackage[utf8]{inputenc}
\usepackage[francais]{babel} 
\usepackage{lipsum}
\usepackage{footnote}
\usepackage{cases}
\selectlanguage{francais}
\usepackage{lastpage}

% insertion d'image
\usepackage{graphicx}
\usepackage{float} % pour le placement des images
\usepackage{subfig} % pour mettre des figures cote-a-cote
\usepackage{epsf} % pour separer une page en deux (minipage)
\usepackage{multicol} % pour creer des colonnes (multicol)
\graphicspath{	{Ressources/images/}
			{Ressources/Logos/}
			{Ressources/Graphiques/}} % Chemin predefinit pour classer les images
\DeclareGraphicsExtensions{.pdf,.png,.jpg} % declaration des extensions pour ne pas les ecrire tout le temps

% style de mise en page
\usepackage{geometry}
\geometry{top=2.5cm, bottom=2.5cm,left=2.3cm, right=2.3cm}
\headheight = 20pt
\usepackage{fancyhdr}
\pagestyle{fancy}
\lhead{\entetegauche}
\chead{}
\rhead{\entetedroite}
\lfoot{}
\cfoot{}
\rfoot{\thepage}

% creation graphique
\usepackage[usenames, dvipsnames]{xcolor}
\usepackage{tikz}
\usetikzlibrary{shapes}

% listings
\usepackage{verbatim}
\usepackage{listings}
%\usepackage{xcolor}
\definecolor{grey}{rgb}{0.96,0.96,0.96}
\definecolor{dkgreen}{rgb}{0,0.6,0}
\definecolor{mauve}{rgb}{0.58,0,0.82}
\definecolor{red}{rgb}{1,0,0}

\lstset{
backgroundcolor=\color{grey}, 
breaklines=true, 
framexleftmargin=1mm, 
xleftmargin=5mm,
xrightmargin=1mm,
showstringspaces=false,
basicstyle=\scriptsize,%\small,
identifierstyle=\normalfont,
% insertion label : //(*\label{comment}*)
}

\lstset{literate=
  {á}{{\'a}}1 {é}{{\'e}}1 {í}{{\'i}}1 {ó}{{\'o}}1 {ú}{{\'u}}1
  {Á}{{\'A}}1 {É}{{\'E}}1 {Í}{{\'I}}1 {Ó}{{\'O}}1 {Ú}{{\'U}}1
  {à}{{\`a}}1 {è}{{\`e}}1 {ì}{{\`i}}1 {ò}{{\`o}}1 {ù}{{\`u}}1
  {À}{{\`A}}1 {È}{{\'E}}1 {Ì}{{\`I}}1 {Ò}{{\`O}}1 {Ù}{{\`U}}1
  {ä}{{\"a}}1 {ë}{{\"e}}1 {ï}{{\"i}}1 {ö}{{\"o}}1 {ü}{{\"u}}1
  {Ä}{{\"A}}1 {Ë}{{\"E}}1 {Ï}{{\"I}}1 {Ö}{{\"O}}1 {Ü}{{\"U}}1
  {â}{{\^a}}1 {ê}{{\^e}}1 {î}{{\^i}}1 {ô}{{\^o}}1 {û}{{\^u}}1
  {Â}{{\^A}}1 {Ê}{{\^E}}1 {Î}{{\^I}}1 {Ô}{{\^O}}1 {Û}{{\^U}}1
  {œ}{{\oe}}1 {Œ}{{\OE}}1 {æ}{{\ae}}1 {Æ}{{\AE}}1 {ß}{{\ss}}1
  {ç}{{\c c}}1 {Ç}{{\c C}}1 {ø}{{\o}}1 {å}{{\r a}}1 {Å}{{\r A}}1
  {€}{{\EUR}}1 {£}{{\pounds}}1
}

\lstdefinestyle{Console}{
	language=c,
	showspaces=false,
	backgroundcolor=	\color{black},
	basicstyle=		\color{green}\scriptsize, 
	keywordstyle=		\color{green}, 
	commentstyle=	\color{green}, 
	stringstyle=		\color{white},
	title=\lstname,
	numbers = left, numberstyle=\tiny\color{black}
	}

\lstdefinestyle{C}{
	language=c, showspaces=false, 
	keywordstyle=		\color{blue}\scriptsize, 
	commentstyle=	\color{dkgreen}\scriptsize\sffamily,  
	stringstyle=		\color{mauve}\scriptsize, 
	title=\lstname,
	escapeinside={//(*}{*)},
	morekeywords={},
	numbers = left, numberstyle=\tiny\color{black}}

\lstdefinestyle{Matlab}{
	language=Matlab, showspaces=false, 
	keywordstyle=		\color{blue}\scriptsize, 
	commentstyle=	\color{dkgreen}\scriptsize\sffamily,  
	stringstyle=		\color{mauve}\scriptsize, 
	title=\lstname,
	escapeinside={(*}{*)},
	morekeywords={},
	numbers = left, numberstyle=\tiny\color{black}}
	
% commandes custom
\providecommand{\abs}[1]{\lvert#1\rvert} % valeur absolue
\providecommand{\norm}[1]{\lVert#1\rVert} % norme
\providecommand{\der}[2]{\frac{\mathrm{d}#1}{\mathrm{d}#2}} % derivee
\newcommand{\tmp}[1]{{\color{red}\textbf{\\#1\\} \marginpar{\color{red}\Huge{\Huge{*}}}}} % note temoraire dans la marge
\newcommand{\tmpnew}[1]{{\color{red}\Huge{*}}\marginpar{\color{red}#1}} % note temoraire dans la marge new
\newcommand{\rem}[1]{\textit{\\ Remarque : {#1}\\}} % note temporaire dans le texte

% Couleur disponibles avec xcolor
%  – De jaune à orange : GreenYellow, Yellow, Goldenrod, Dandelion, Apricot, Peach, Melon, YellowOrange,
%  – De orange à rouge : Orange, BurntOrange, Bittersweet, RedOrange, Mahogany, Maroon, BrickRed, Red,
%  – De rouge à rose : OrangeRed, RubineRed, WildStrawberry, Salmon, CarnationPink, Magenta, VioletRed, Rhodamine,
%  – De rose à violet : Mulberry, RedViolet, Fuchsia, Lavender, Thistle, Orchid, DarkOrchid, Purple,
%  – De violet à bleu : Plum, Violet, RoyalPurple, BlueViolet, Periwinkle, CadetBlue, CornflowerBlue, MidnightBlue,
%  – De bleu à bleu clair : NavyBlue, RoyalBlue, Blue, Cerulean, Cyan, ProcessBlue, SkyBlue, Turquoise
%  – De bleu clair à vert : TealBlue, Aquamarine, BlueGreen, Emerald, JungleGreen, SeaGreen, Green, ForestGreen,
%  – De vert à brun : PineGreen, LimeGreen, YellowGreen, SpringGreen, OliveGreen, RawSienna, Sepia, Brown, Tan

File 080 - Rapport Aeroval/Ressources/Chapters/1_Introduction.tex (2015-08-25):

% Chapter Template

\chapter{Introduction} % Main chapter title

\label{Chapitre 1} % Change X to a consecutive number; for referencing this chapter elsewhere, use \ref{ChapterX}

\lhead{ \emph{Introduction}} % Change X to a consecutive number; this is for the header on each page - perhaps a shortened title

Ce document présente la conception d'une carte électronique destinée à permettre le contrôle d'un multicoptère.
\\
Cette carte a été conçue pour permettre le test de différents algorithmes de mesure d'attitude, de position et de régulation, en utilisants plusieurs capteurs différents dans le but de permettre le pilotage assisté d'un multicoptère.
\\
Afin de rendre le pilotage plus simple pour l'utilisateur, voire même, de l'automatiser complètement dans un second temps à l'aide d'un GPS, les sorties des moteurs doivent être calculées et régulées

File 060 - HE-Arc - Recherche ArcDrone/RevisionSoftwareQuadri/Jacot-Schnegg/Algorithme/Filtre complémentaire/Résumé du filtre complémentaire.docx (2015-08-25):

Résumé du filtre complémentaire :

1er ordre

Soit les deux filtres passe-bas et passe-haut suivants :

Par exemple, a=0.02 et b=0.98. On constate que Hlp(z)+Hhp(z)=1, donc les filtres sont complémentaires. On applique le passe-bas sur l’angle donné par l’accéléromètre et le passe-haut sur l’angle donné par le gyroscope.

On trouve l’équation aux différences du domaine temporel :

Le dernier terme, celui qui est entre les crochets, est très intéressant. En effet, on ne mesure pas θgyr directement, mais sa dérivée θrate en rad/s! On pose donc (Ts = période d’échantillonnage) :

On pose enfin :

Comment choisir le paramètre a (note: b = 1-a) ? On considère la constante de temps τ :

En-dessous de τ, le passe-bas prédomine. En dessus de τ, c’est le passe-haut qui prédomine. En principe a est petit et b proche de 1.

Problème avec un filtre complémentaire du 1er ordre

Reprenons la fonction de tranfert en z, mais en considérant θgyr comme l’intégration de θrate au cours du temps. On a donc θgyr(n) =θgyr(n-1)+ θrate(n)·Ts. Dans Z, on obtient :

On conclut :

Si on a un biais θrate = θconst, on obtient une erreur statique

C’est la raison pour laquelle on préfère parfois un filtre du deuxième ordre.

2ème ordre

On peut prendre la solution suivante :

On trouve :

En tenant compte de l’intégration de θgyr on trouve :

L’erreur statique a disparu, au prix d’une plus grande complexité de réalisation. L’inconvénient de cette solution est le plus grand retard du filtre. L’équation aux différences de notre exemple donne :

Bien entendu, tous les paramètres constants (par exemple 2b·(1-b)) sont calculés à l’avance.

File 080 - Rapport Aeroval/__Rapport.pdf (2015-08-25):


# Aeroval

## Développement d’une carte électronique le contrôle d’un multicoptère

Valentin Py

2015

HE-Arc
Systèmes embarqués

Dernière mise à jour : 3 juillet 2015

# Table des matières

1 Introduction | 1
2 Nom du chaptitre | 2
3 Nom du chaptitre | 4
4 Conclusion | 6

I

# Chapitre 1

# Introduction

Ce document présente la conception d’une carte électronique destinée à permettre le contrôle d’un multicoptère.
Cette carte a été conçue pour permettre le test de différents algorithmes de mesure d’attitude, de position et de régulation, en utilisants plusieurs capteurs différents dans le but de permettre le pilotage assisté d’un multicoptère.
Afin de rendre le pilotage plus simple pour l’utilisateur, voire même, de l’automatiser complètement dans un second temps à l’aide d’un GPS, les sorties des moteurs doivent être calculées et régulées

# Chapitre 2

# Nom du chaptitre

Introduction chapitre

## 2.1 Nom de la section

Texte section.

### 2.1.1 Titre sous section

Texte sous section

1 | i n t main ( )
2 | {
3 | p r i n t f ( " exemple en C\n" ) ;
4 | r e t u r n 0 ;
5 | }

Exemple de texte.

main.c

1 #i n cl u d e <s t d i o . h>

2
3 | i n t main ( )
4 | {
5 | p r i n t f ( " H ell o world \n" ) ;
6 | r e t u r n 0 ;
7 | }

Texte
Remarque : Ceci est une remarque
*

tmp new :
A faire !

1 $ Texte c o n s ol e

Nom du chaptitre | Développement d’une carte électronique le contrôle d’un multicoptère

Apès un saut de page.

Texte
Liste


1. Premier
2. Deuxième
3. Dernier

# Chapitre 3

# Nom du chaptitre

Introduction chapitre

## 3.1 Nom de la section

Texte section.

### 3.1.1 Titre sous section

Texte sous section

1 | i n t main ( )
2 | {
3 | p r i n t f ( " exemple en C\n" ) ;
4 | r e t u r n 0 ;
5 | }

Exemple de texte.

main.c

1 #i n cl u d e <s t d i o . h>

2
3 | i n t main ( )
4 | {
5 | p r i n t f ( " H ell o world \n" ) ;
6 | r e t u r n 0 ;
7 | }

Texte
Remarque : Ceci est une remarque
*

tmp new :
A faire !

1 $ Texte c o n s ol e

Nom du chaptitre | Développement d’une carte électronique le contrôle d’un multicoptère

Apès un saut de page.

Texte
Liste
1. Premier
2. Deuxième
3. Dernier

# Chapitre 4

# Conclusion

Exemple de conclusion

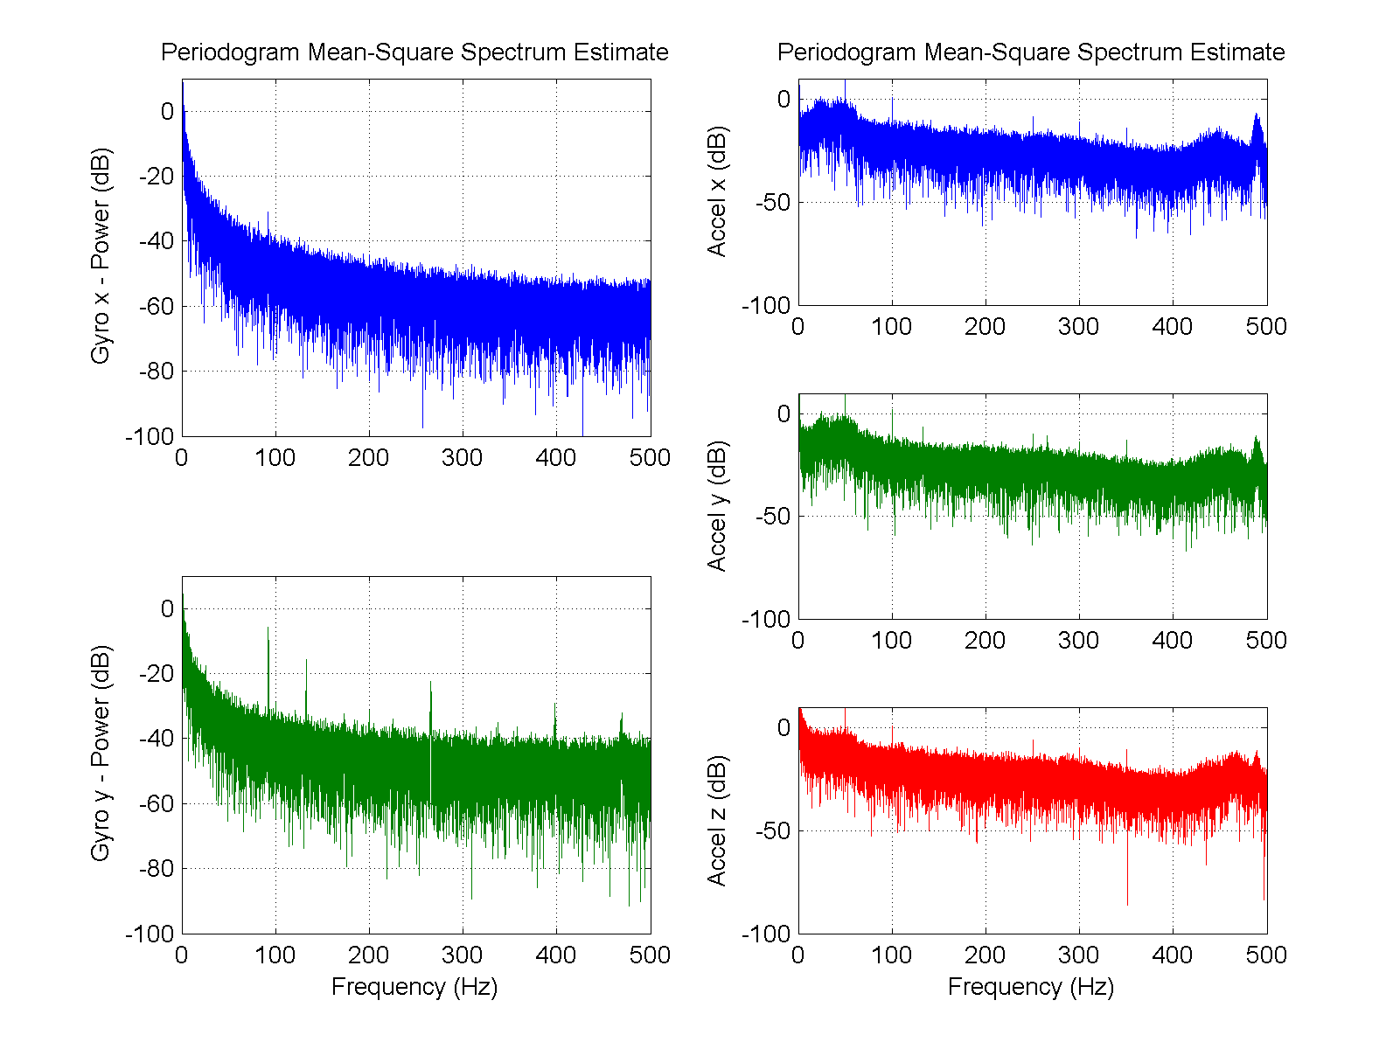
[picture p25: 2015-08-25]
060 - HE-Arc - Recherche ArcDrone/RevisionSoftwareQuadri/Jacot-Schnegg/Algorithme/Simulink/dataSpectralAnalysis.png

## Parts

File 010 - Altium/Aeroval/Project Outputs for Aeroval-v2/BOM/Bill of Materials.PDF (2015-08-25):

Component list | Aeroval-v2.PrjPcb
Source Data From: | | Aeroval-v2.PrjPcb
Project: | | Aeroval-v2.PrjPcb
Variant: | | <Parameter Revision not found>
Report Date: | 22.08.2015 | 16:38:45
Print Date: | 22-Aug-15 | 4:39:05 PM
Comment | Description | Quantity | Footprint | Designator | Manufacturer 1 | Manufacturer Part Number 1 | Supplier 1 | Supplier Part Number 1 | Supplier Unit Price 1 | Supplier Subtotal 1 | Value
100nF | CAP CER 0.1UF 25V 10% X7R 0805 | 33 | 080503 | C1, C5, C9, C10, C13, C14, C15, C18, C19, C20, C29, C30, C31, C34, C36, C37, C38, C39, C41, C43, C45, C47, C48, C49, C50, C51, C52, C53, C54, C55, C56, C58, C59 | Samsung Electro-Mechanics America, Inc. | CL21B104KACNNNC | Digi-Key | 1276-1099-1-ND | 0,0204 | 6 732 | 100nF
1uF | CAP CER 1UF 25V 10% X7R 0805 | 14 | 080503 | C2, C3, C4, C6, C7, C8, C11, C12, C16, C17, C23, C24, C27, C32 | Kemet | C0805C104K3RACTU | Digi-Key | 399-1168-1-ND | 0,023 | 3,22 | 1uF
10uF | CAP CER 10UF 16V 20% X6S 0805 | 2 | 080501 | C21, C22 | TDK Corporation | C2012X6S1C106M125AC | Digi-Key | 445-7612-1-ND | 0,35 | 7 | 10uF
10nF | CAP CER 10nF 50V 10% X7R 0805 | 2 | 080503 | C25, C33 | Kemet | C0805C103K5RACTU | Digi-Key | 399-1158-1-ND | 0,034 | 0,68 | 10nF
220uF | CAP TANT 220UF 4V 20% 1411 | 1 | 1411 | C26 | Kemet | T491B227M004AT | Digi-Key | 399-4625-6-ND | 0,956 | 9,56 | 220uF
22uF | CAP TANT 22UF 25V 10% 2413 | 1 | 2413 | C28 | Kemet | T491C226K025AT | Digi-Key | 399-3746-1-ND | 0,888 | 8,88 | 22uF
2.2nF | CAP CER 2.2nF 50V | 1 | 080503 | C35 | Kemet | C0805C222F5GACTU | Digi-Key | 399-11167-2-ND | | | 2.2nF
4.7uF | CAP TANT 4.7uF 10V 10% 1206 | 2 | 120605 | C40, C44 | Kemet | T491A475K010AT | Digi-Key | 399-3696-1-ND | 0,30 | 6 | 4.7uF
220nF | CAP CER 0.22uF 50V X7R 10% 0805 | 2 | 080503 | C42, C46 | Kemet | C0805C224K5RACTU | Digi-Key | 399-3491-1-ND | 0,095 | 1,9 | 220nF
10uF | CAP CER 10UF 16V 20% X6S 0805 | 1 | 080503 | C57 | TDK Corporation | C2012X6S1C106M125AC | Digi-Key | 445-7612-1-ND | 0,35 | 3,5 | 10uF
18pF | CAP CER 18PF 50V 5% NP0 0603 | 2 | 060301 | C60, C61 | Kemet | C0603C180J5GACTU | Digi-Key | 399-1052-6-ND | 0,034 | 0,68 | 18pF
SP0504BAHTG | TVS AVAL DIODE ARRAY 4CH, 5.5V | 1 | SOT23501 | D1 | Littelfuse Inc. | SP0504BAHTG | Digi-Key | F3157CT-ND | 0,899 | 8,99
LED | LED 2X1.2MM 570NM GN WTR CLR SMD | 9 | LED_0805 -GREEN | D2, D3, D4, D5, D6, D7, D8, D9, D10 | Kingbright | APT2012CGCK | Digi-Key | 754-1127-1-ND | 0,28 | 25,2
TVS DIODE 3.3V | TVS DIODE 3.3VWM 8VC SOD523 | 10 | SOD-523 | D11, D13, D14, D15, D16, D17, D18, D19, D20, D21 | Comchip Technology | CPDH3V3UP | Digi-Key | 641-1395-1-ND | 0,3708 | 37,08
B230A-13-F | B230A-13-F | 1 | SMA | D12 | Diodes Incorporated | B230A-13-F | Digi-Key | B230A-FDICT-ND | 0,38 | 3,8 | 500mV
EM7180SFP | | 1 | EM7180SFP | EM1
BLM21BB331SN1D | EMI Filter Beads, Chips & Arrays 0805 330 OHM | 1 | 080501 | FB1 | Murata Electronics | BLM21BB331SN1D | Mouser | 81-BLM21BB331SN1D | 0,085 | 0,85 | 300R@100MHz
CONN_4 | [NoValue], CONN HEADER 2.54mm 4, [NoValue], CONN HEADER 2.54mm 4 | 4 | 640454-4 | J1, J3, J4, J9
CONN_2 | CONN HEADER 2.54mm 2 | 8 | 640454-2 | J2, J6, J8, J11, J24, J25, J26, J47 | | | Stock
UX60-MB-5ST | CONN RECEPT MINI B USB2.0 | 1 | USB/UX60-MB-5ST | J5 | Hirose Electric Co Ltd | UX60-MB-5ST | Digi-Key | H2959CT-ND | 0,944 | 9,44
CONN_6 | | 4 | 640454-6 | J7, J10, J12, J15
CONN_3 | CONN HEADER 2.54mm 3 | 26 | 640454-3 | J13, J14, J16, J17, J19, J20, J27, J28, J29, J30, J31, J32, J33, J34, J35, J36, J37, J38, J39, J40, J41, J42, J43, J44, J45, J46 | | | Stocks, Stocks, Stocks, Stock, Stocks, Stock, Stock, Stock, Stock, Stock, Stock, Stock, Stock, Stock, Stock, Stock, Stock, Stock, Stock, Stock, Stock, Stock, Stock, Stock, Stock, Stock
CONN_10 | | 1 | 640454-10 | J18
CONN_SD | CON 8 SD CARD PUSH SMT 1.1MM SP 75H AU | 1 | con8_sdcard_ push_sm | J21 | Molex Inc. | 1050270001 | Digi-Key | WM6825CT-ND | 1 261 | 12,61
FTSH-105-01-F-DV-K | CONN HEADER 10POS DUAL .05" SMD | 1 | FTSH-105-01-F-DV-K | J22 | Samtec Inc. | FTSH-105-01-F-DV-K | Digi-Key | FTSH-105-01-F-DV-K-ND | 3,02 | 30,2
CONN_BAT | TERM BLOCK HDR 2POS R/A 5.08MM | 1 | SL508_2C | J23 | Weidmuller | 1514910000 | Digi-Key | 281-1279-ND | 0,486 | 4,86 | 282857-2
82uH | SDR1307-820KL | 1 | L1 | L1 | Bourns Inc. | SDR1307-820KL | Digi-Key | SDR1307-820KLCT-ND | 0,78 | 7,8 | 82uH
HMC5983 | IC COMPASS 3 AXIS 16-LCC | 2 | QFN16 | MAG1, MAG2 | Honeywell Microelectronics & Precision Sensors | HMC5983-TR | Digi-Key | 342-1092-1-ND | 2 303 | 46,06
MPU-6000 | GYRO/ACCELEROMETER 6AXIS 24QFN | 1 | QFN24 | MPU1 | InvenSense | MPU-6000 | Digi-Key | 1428-1005-1-ND | 8 465 | 84,65
MS5611 | | 1 | MS5611 | MSC1
1.69k | RES 1.69K OHM 1% 1/8W 0805 | 5 | 060301 | R1, R3, R4, R5, R37 | Panasonic Electronic Components | ERJ-3EKF1691V | Digi-Key | P1.69KHCT-ND | 0,0114 | 0,57 | 1.69K
4k7 | RES 4.7K 0805, RES 4.7K 0805, RES 4.7K 0805, RES 4.7K 0805, RES 4.7K 0805, RES 4.7K 0805, RES 4.7K 0805, RES 4.7K 0805, RES 4.7K 0805, RES 4.7K 1% 0603, RES 4.7K 0805, RES 4.7K 0805, RES 4.7K 0805, RES 4.7K 0805, RES 4.7K 0805, RES 4.7K 0805, RES 4.7K 0805 | 17 | 060301 | R2, R11, R12, R13, R14, R21, R22, R23, R24, R33, R58, R59, R60, R61, R62, R63, R64 | Stackpole Electronics Inc. | RMCF0603FT4K70 | Digi-Key | RMCF0603FT4K70CT-ND | 0,0105 | 1 785 | 4k7
220R | RES 220R 0805 | 8 | 060301 | R6, R7, R8, R15, R16, R17, R18, R25 | Stackpole Electronics Inc. | RMCF0603FT220R | Digi-Key | RMCF0603FT220RCT-ND | 0,0138 | 1 104 | 220R
15k | RES 15K 0805 | 7 | 060301 | R9, R10, R19, R20, R26, R27, R65 | Rohm Semiconductor | MCR03ERTF1502 | Digi-Key | RHM15.0KCFCT-ND | 0,016 | 1,12 | 15k
10k | RES 10K 0805 | 4 | 060301 | R28, R30, R31, R66 | Rohm Semiconductor | MCR03ERTF1002 | Digi-Key | RHM10.0KCFCT-ND | 0,016 | 0,64 | 10k
2k2 | RES 2.2k 0805 | 2 | 060301 | R29, R32 | Stackpole Electronics Inc. | RMCF0603FT2K20 | Digi-Key | RMCF0603FT2K20CT-ND | 0,025 | 0,5 | 2k2
2k | RES 2K 1% 0805 | 1 | 060301 | R34 | Panasonic Electronic Components | ERJ-3EKF2001V | Digi-Key | P2.00KHCT-ND | 0,10 | 1 | 2k
1k | RES 1k 0805 | 2 | 060301 | R35, R36 | Panasonic Electronic Components | ERJ-3EKF1001V | Digi-Key | P1.00KHDKR-ND | 0,10 | 2 | 1k
330R | RES 330R 0805 | 8 | 060301 | R38, R39, R40, R41, R42, R43, R44, R45 | Rohm Semiconductor | MCR03ERTF3300 | Digi-Key | RHM330CFCT-ND | 0,016 | 1,28 | 330R
1M | RES 1M 0603 | 1 | 060301 | R67 | Yageo | RC0603FR-071ML | Digi-Key | 311-1.00MHRCT-ND | 0,014 | 0,14 | 1M
SWITCH | SWITCH DIP TOP SLIDE 4POS SMD | 2 | GDS04 | SW1, SW2 | C&K Components | SDA04H1SBD | Digi-Key | CKN6068-ND | 1 644 | 32,88
EVQ-PAG05R | SWITCH LT 6MM 260GF 5MM HEIGHT | 1 | EVQ-PAG05R | SW3 | Panasonic Electronic Components | EVQ-PAG05R | Digi-Key | P12195S-ND | 0,256 | 2,56 | EVQ-PAG05R
BCV27 | TRANS NPN DARL 30V 1.2A SOT23 | 4 | BCV27 | T1, T2, T3, T4 | Fairchild Semiconductor | BCV27 | Digi-Key | BCV27CT-ND | 0,15 | 6
CP2102 | Single-Chip USB to UART Bridge | 1 | QFN-28 | U1 | Silicon Labs | CP2102-GM | Digi-Key | 336-1160-5-ND | 2,75 | 27,5
NCV1117ST50T3G | Low Dropout (LDO) Regulators ANA 800mA LDO | 1 | SOT223 | U2 | ON Semiconductor | NCV1117ST50T3G | Digi-Key | NCV1117ST50T3GOSCT-ND | 0,872 | 8,72
REG1117-3.3/2K5 | IC REG LDO 3.3V 0.8A SOT223 | 1 | SOT223 | U3 | Texas Instruments | REG1117-3.3/2K5 | Digi-Key | 296-21321-1-ND | 1,63 | 16,3
LM2596 | IC REG BUCK ADJ 3A TO263-5 | 1 | TO263 | U4 | Texas Instruments | LM2596SX-ADJ/NOPB | Digi-Key | 296-35399-1-ND | 4,05 | 40,5
SN74LV4T125 | IC BUFF/DVR NON-INVERT 14TSSOP | 3 | TSSOP14 | U5, U6, U7 | Texas Instruments | SN74LV4T125PWR | Digi-Key | 296-40545-1-ND | 0,8064 | 24 192
MK64FN1M0VLQ12 | MK64FN1M0VLQ12 | 1 | LQFP 144 | uC1 | Freescale Semiconductor | MK64FN1M0VLQ12 | Digi-Key | MK64FN1M0VLQ12-ND | 11 526 | 115,26
CRYSTAL 32.768k | CRYSTAL 32.768 KHZ 12.5PF SMD | 1 | XT-5 | Y1 | ECS Inc. | ECS-.327-12.5-17X-C-TR | Digi-Key | XC1912CT-ND | 1 073 | 10,73 | 32.768kHz
ABM3-8.000MHZ-D2Y-T | CRYSTAL 8MHZ 18PF SMD | 1 | XT8_2-SMD | Y2 | Abracon LLC | ABM3-8.000MHZ-D2Y-T | Digi-Key | 535-10630-6-ND | 0,968 | 9,68 | 8 MHz

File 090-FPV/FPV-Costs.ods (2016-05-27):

Fournisseur | Description | Quantité Total | Quantité Vincent | Quantité Val | Prix Total | Prix Vincent | Prix Val | Etat | Payé par Vincent | Payé par Valentin | Lien
Bangood | OSD | 2 | 1 | 1 | 18.08 | 9.04 | 9.04 | Reçu | 1 | 0 | http://www.banggood.com/fr/MICRO-MinimOSD-Minim-OSD-Mini-OSD-W-KV-Team-MOD-For-Naze32-Flight-Controller-p-990556.html
Bangood | TX 200mW | 2 | 1 | 1 | 50.66 | 25.33 | 25.33 | Reçu | 1 | 0 | http://www.banggood.com/AOMWAY-FPV-5_8Ghz-200mW-32CH-Wireless-AV-Transmitter-Module-p-947147.html
Bangood | Rallonge antenne 5cm | 2 | 1 | 1 | 4.16 | 2.08 | 2.08 | Reçu | 1 | 0 | http://www.banggood.com/FPV-5cm-Extension-Cable-SMA-Male-to-SMA-Female-Right-Angle-Cable-p-1022382.html
Bangood | Rallonge antenne 10cm | 2 | 1 | 1 | 5.46 | 2.73 | 2.73 | Reçu | 1 | 0 | http://www.banggood.com/10cm-SMA-Male-Plug-to-SMA-Female-Jack-Bulkhead-Right-Angle-Pigtail-Cable-RG316-p-985300.html
Bangood | Adaptateurs antennes | 4 | 2 | 2 | 6.04 | 3.02 | 3.02 | Reçu | 1 | 0 | http://www.banggood.com/SMA-Male-to-RP-SMA-Female-Right-Angle-RF-Adapter-Connector-p-940599.html
Bangood | PCB Leds | 1 | 1 | 0 | 7.59 | 7.59 | 0 | Reçu | 1 | 0 | http://www.banggood.com/Matek-PDB-BEC-5V-3A-LED-Lighting-Control-Tracker-Low-Voltage-Alarm-LED-POWER-HUB-5in1-p-991017.html
Bangood | Buzzer | 9 | 9 | 0 | 3.03 | 3.03 | 0 | Reçu | 1 | 0 | http://www.banggood.com/10Pcs-5V-Electromagnetic-Active-Buzzer-Continuous-Beep-Continuously-p-943524.html
Bangood | LEDS – ruban | 1 | 0 | 1 | 4.35 | 0 | 4.35 | Reçu | 1 | 0 | http://www.banggood.com/Matek-8-Bit-WS2812B-RGB-5050-Highlight-LED-for-Naze32-CC3D-p-983608.html
Bangood | LEDS – carré | 2 | 0 | 2 | 2 | 0 | 2 | Reçu | 1 | 0 | http://www.banggood.com/4W-48led-COB-LED-Chip-480mA-WhiteWarm-White-For-DIY-DC-12V-p-959059.html
Bangood | LC | 6 | 3 | 3 | 13.62 | 6.81 | 6.81 | Reçu | 1 | 0 | http://www.banggood.com/L-C-Power-Filter-2A-RTF-LC-FILTER-3AMP-2-4S-LC-Module-Lllustrated-Eliminate-Moire-Video-Signal-p-1029694.html
Bangood | Visserie | 1 |  |  |  |  |  | Reçu
Bangood | Paracorde | 1 |  |  |  |  |  | Reçu | 1 | 0 | http://www.banggood.com/50ft-9Core-Strand-550Lb-Luminous-Glow-Nylon-Paracord-Parachute-Rope-p-923088.html
Bangood | Frais de port Banggood | 0 |  |  |  |  |  | n/d | 1 | 0
Dronefactory | Fatshark | 2 | 1 | 1 | 788 | 394 | 394 | Reçu 1/2 | 0 | 1 | http://www.dronefactory.ch/dronefactory-shop/fatshark-dominator-v3-video-brille/
Dronefactory | Antennes | 4 | 2 | 2 | 80 | 40 | 40 | Reçu | 0 | 1 | http://www.dronefactory.ch/dronefactory-shop/tbs-triumph-5-8ghz-antenna-rp-sma/
Dronefactory | Frais de port | 1 | 0.5 | 0.5 | 36 | 18 | 18 | n/d | 0 | 1
Aerodron | RX | 2 | 1 | 1 | 69.8 | 34.9 | 34.9 | Début mars | 0 | 1 | https://shop.aerodron.ch/en/fk0035.html
Aerodron | Frais de port | 1 | 0.5 | 0.5 | 12.5 | 6.25 | 6.25 | n/d | 0 | 1
Specialcopter | Caméra | 2 | 1 | 1 | 118 | 59 | 59 | Reçu | 0 | 1 | https://specialcopter.ch/shop/Multikopter-FPV/FatShark/FS-960TVL-Cam.html
Specialcopter | Prop balancer | 1 | 0 | 1 | 14.9 | 0 | 14.9 | Reçu | 0 | 1 | https://specialcopter.ch/shop/Accessoires/propbalancer.html
Specialcopter | Frais de port | 1 | 0.5 | 0.5 | 9.9 | 4.95 | 4.95 | n/d | 0 | 1
Total |  | 47 | 25.5 | 19.5 | 1244.09 | 616.73 | 627.36 |  | 59.63 | 1129.1

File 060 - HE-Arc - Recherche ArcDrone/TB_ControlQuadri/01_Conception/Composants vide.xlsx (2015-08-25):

Référence | Article | Désignation | Technologie | Tension | Courant | Puissance | Précision | Fabricant | Référence | Fournisseur | Référence | Document | Boîtier | Prix
schéma |  |  |  | (V) | (A) | (W) | (%) |  | fabricant |  | fournisseur | pdf |  | 1 | 10
Composants passifs
 |  |  |  |  |  |  |  |  |  |  |  | Prix partiel |  | 0.00 | 0.00
Semiconducteurs discrets
 |  |  |  |  |  |  |  |  |  |  |  | Prix partiel |  | 0.00 | 0.00
Circuits intégrés
 |  |  |  |  |  |  |  |  |  |  |  | Prix partiel |  | 0.00 | 0.00
Electromécanique
 | M icro |  | condensateur électret | 10 | 0.5 |  |  | CUI inc | CMA-4544PF-W | Digikey | 102-1721-ND
 |  |  |  |  |  |  |  |  |  |  |  | Prix partiel |  | 0.00 | 0.00
PCB
 |  |  |  |  |  |  |  |  |  |  |  |  |  | 0.00 | 0.00
 |  |  |  |  |  |  |  |  |  |  |  | Prix partiel |  | 0.00 | 0.00
 |  |  |  |  |  |  |  |  |  |  | Prix totaux |  |  | 0.00 | 0.00

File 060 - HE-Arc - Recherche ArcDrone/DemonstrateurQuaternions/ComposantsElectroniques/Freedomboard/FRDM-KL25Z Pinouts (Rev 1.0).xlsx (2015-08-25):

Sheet: KL25Z Pinouts
FRDM-KL25Z Pin usage and pinout chart
FRDM-KL25Z Pins |  |  |  | KL25Z128 Pins
On-board Usage | I/O Header & Pin Num | Arduino™ R3 Pin Name | FRDM-KL25Z Pin Name | KL25Z Pin # | ALT0 | ALT1 | ALT2 | ALT3 | ALT4 | ALT5 | ALT6 | ALT7 | Reset State/Function
― | J2 20 | D14 | PTE0 | 1 |  | PTE0 |  | UART1_TX | RTC_CLKOUT | CMP0_OUT | I2C1_SDA |  | DISABLED
― | J2 18 | D15 | PTE1 | 2 |  | PTE1 | SPI1_MOSI | UART1_RX |  | SPI1_MISO | I2C1_SCL |  | DISABLED
― | J9 09 | ― | PTE2 | 3 |  | PTE2 | SPI1_SCK |  |  |  |  |  | DISABLED
― | J9 11 | ― | PTE3 | 4 |  | PTE3 | SPI1_MISO |  |  | SPI1_MOSI |  |  | DISABLED
― | J9 13 | ― | PTE4 | 5 |  | PTE4 | SPI1_PCS0 |  |  |  |  |  | DISABLED
― | J9 15 | ― | PTE5 | 6 |  | PTE5 |  |  |  |  |  |  | DISABLED
Power | ― | ― | VDD | 7 | VDD |  |  |  |  |  |  |  | VDD
Power | ― | ― | VSS | 8 | VSS |  |  |  |  |  |  |  | VSS
USB | ― | ― | USB0_DP | 9 | USB0_DP |  |  |  |  |  |  |  | USB0_DP
USB | ― | ― | USB0_DM | 10 | USB0_DM |  |  |  |  |  |  |  | USB0_DM
2.2uF cap | ― | ― | VOUT33 | 11 | VOUT33 |  |  |  |  |  |  |  | VOUT33
USB VBUS (5V) | ― | ― | VREGIN | 12 | VREGIN |  |  |  |  |  |  |  | VREGIN
― | J10 01 | ― | PTE20 | 13 | ADC0_DP0/ADC0_SE0 | PTE20 |  | FTM1_CH0 | UART0_TX |  |  |  | ADC0_DP0/ADC0_SE0
― | J10 03 | ― | PTE21 | 14 | ADC0_DM0/ADC0_SE4a | PTE21 |  | FTM1_CH1 | UART0_RX |  |  |  | ADC0_DM0/ADC0_SE4a
― | J10 05 | ― | PTE22 | 15 | ADC0_DP3/ADC0_SE3 | PTE22 |  | FTM2_CH0 | UART2_TX |  |  |  | ADC0_DP3/ADC0_SE3
― | J10 07 | ― | PTE23 | 16 | ADC0_DM3/ADC0_SE7a | PTE23 |  | FTM2_CH1 | UART2_RX |  |  |  | ADC0_DM3/ADC0_SE7a
Power | ― | ― | VDDA | 17 | VDDA |  |  |  |  |  |  |  | VDDA
Power | J2 16 | AREF* | VREFH | 18 | VREFH |  |  |  |  |  |  |  | VREFH
Power | ― | ― | VREFL | 19 | VREFL |  |  |  |  |  |  |  | VREFL
Power | ― | ― | VSSA | 20 | VSSA |  |  |  |  |  |  |  | VSSA
― | J10 09 | ― | PTE29 | 21 | CMP0_IN5/ADC0_SE4b | PTE29 |  | FTM0_CH2 | FTM_CLKIN0 |  |  |  | CMP0_IN5/ADC0_SE4b
― | J10 11 | ― | PTE30 | 22 | DAC0_OUT/ADC0_SE23/CMP0_IN4 | PTE30 |  | FTM0_CH3 | FTM_CLKIN1 |  |  |  | DAC0_OUT/ADC0_SE23/CMP0_IN4
― | J2 13 | ― | PTE31 | 23 |  | PTE31 |  | FTM0_CH4 |  |  |  |  | DISABLED
Accelerometer I2C | ― | ― | PTE24 | 24 |  | PTE24 |  | FTM0_CH0 |  | I2C0_SCL |  |  | DISABLED
Accelerometer I2C | ― | ― | PTE25 | 25 |  | PTE25 |  | FTM0_CH1 |  | I2C0_SDA |  |  | DISABLED
Debug (SWD_CLK) | ― | ― | PTA0 | 26 | TSI0_CH1 | PTA0 |  | FTM0_CH5 |  |  |  | SWD_CLK | SWD_CLK
― | J1 02 | D0 | PTA1 | 27 | TSI0_CH2 | PTA1 | UART0_RX | FTM2_CH0 |  |  |  |  | DISABLED
― | J1 04 | D1 | PTA2 | 28 | TSI0_CH3 | PTA2 | UART0_TX | FTM2_CH1 |  |  |  |  | DISABLED
Debug (SWD_DIO) | ― | ― | PTA3 | 29 | TSI0_CH4 | PTA3 | I2C1_SCL | FTM0_CH0 |  |  |  | SWD_DIO | SWD_DIO
― | J1 10 | D4 | PTA4 | 30 | TSI0_CH5 | PTA4 | I2C1_SDA | FTM0_CH1 |  |  |  | NMI_b | NMI_b
― | J1 12 | D5 | PTA5 | 31 |  | PTA5 | USB_CLKIN | FTM0_CH2 |  |  |  |  | DISABLED
― | J1 08 | D3 | PTA12 | 32 |  | PTA12 |  | FTM1_CH0 |  |  |  |  | DISABLED
― | J2 02 | D8 | PTA13 | 33 |  | PTA13 |  | FTM1_CH1 |  |  |  |  | DISABLED
Accelerometer INT1 | ― | ― | PTA14 | 34 |  | PTA14 | SPI0_PCS0 | UART0_TX |  |  |  |  | DISABLED
Accelerometer INT2 | ― | ― | PTA15 | 35 |  | PTA15 | SPI0_SCK | UART0_RX |  |  |  |  | DISABLED
― | J2 09 | ― | PTA16 | 36 |  | PTA16 | SPI0_MOSI |  |  | SPI0_MISO |  |  | DISABLED
― | J2 11 | ― | PTA17 | 37 |  | PTA17 | SPI0_MISO |  |  | SPI0_MOSI |  |  | DISABLED
Power | ― | ― | VDD | 38 | VDD |  |  |  |  |  |  |  | VDD
Power | ― | ― | VSS | 39 | VSS |  |  |  |  |  |  |  | VSS
8MHz XTAL | ― | ― | PTA18 | 40 | EXTAL0 | PTA18 |  | UART1_RX | FTM_CLKIN0 |  |  |  | EXTAL0
8MHz XTAL | ― | ― | PTA19 | 41 | XTAL0 | PTA19 |  | UART1_TX | FTM_CLKIN1 |  | LPTMR0_ALT1 |  | XTAL0
Reset | J9 06 | ― | PTA20 | 42 |  | PTA20 |  |  |  |  |  | RESET_b | RESET_b
― | J10 02 | A0 | PTB0 | 43 | ADC0_SE8/TSI0_CH0 | PTB0/LLWU_P5 | I2C0_SCL | FTM1_CH0 |  |  |  |  | ADC0_SE8/TSI0_CH0
― | J10 04 | A1 | PTB1 | 44 | ADC0_SE9/TSI0_CH6 | PTB1 | I2C0_SDA | FTM1_CH1 |  |  |  |  | ADC0_SE9/TSI0_CH6
― | J10 06 | A2 | PTB2 | 45 | ADC0_SE12/TSI0_CH7 | PTB2 | I2C0_SCL | FTM2_CH0 |  |  |  |  | ADC0_SE12/TSI0_CH7
― | J10 08 | A3 | PTB3 | 46 | ADC0_SE13/TSI0_CH8 | PTB3 | I2C0_SDA | FTM2_CH1 |  |  |  |  | ADC0_SE13/TSI0_CH8
― | J9 01 | ― | PTB8 | 47 |  | PTB8 |  | EXTRG_IN |  |  |  |  | DISABLED
― | J9 03 | ― | PTB9 | 48 |  | PTB9 |  |  |  |  |  |  | DISABLED
― | J9 05 | ― | PTB10 | 49 |  | PTB10 | SPI1_PCS0 |  |  |  |  |  | DISABLED
― | J9 07 | ― | PTB11 | 50 |  | PTB11 | SPI1_SCK |  |  |  |  |  | DISABLED
Touch Slider | ― | ― | PTB16 | 51 | TSI0_CH9 | PTB16 | SPI1_MOSI | UART0_RX | FTM_CLKIN0 | SPI1_MISO |  |  | TSI0_CH9
Touch Slider | ― | ― | PTB17 | 52 | TSI0_CH10 | PTB17 | SPI1_MISO | UART0_TX | FTM_CLKIN1 | SPI1_MOSI |  |  | TSI0_CH10
Red LED | ― | ― | PTB18 | 53 | TSI0_CH11 | PTB18 |  | FTM2_CH0 |  |  |  |  | TSI0_CH11
Green LED | ― | ― | PTB19 | 54 | TSI0_CH12 | PTB19 |  | FTM2_CH1 |  |  |  |  | TSI0_CH12
― | J1 03 | ― | PTC0 | 55 | ADC0_SE14/TSI0_CH13 | PTC0 |  | EXTRG_IN |  | CMP0_OUT |  |  | ADC0_SE14/TSI0_CH13
― | J10 12 | A5 | PTC1 | 56 | ADC0_SE15/TSI0_CH14 | PTC1/LLWU_P6/RTC_CLKIN | I2C1_SCL |  | FTM0_CH0 |  |  |  | ADC0_SE15/TSI0_CH14
― | J10 10 | A4 | PTC2 | 57 | ADC0_SE11/TSI0_CH15 | PTC2 | I2C1_SDA |  | FTM0_CH1 |  |  |  | ADC0_SE11/TSI0_CH15
― | J1 05 | ― | PTC3 | 58 |  | PTC3/LLWU_P7 |  | UART1_RX | FTM0_CH2 | CLKOUT |  |  | DISABLED
Power | ― | ― | VSS | 59 | VSS |  |  |  |  |  |  |  | VSS
Power | ― | ― | VDD | 60 | VDD |  |  |  |  |  |  |  | VDD
― | J1 07 | ― | PTC4 | 61 |  | PTC4/LLWU_P8 | SPI0_PCS0 | UART1_TX | FTM0_CH3 |  |  |  | DISABLED
― | J1 09 | ― | PTC5 | 62 |  | PTC5/LLWU_P9 | SPI0_SCK | LPTMR0_ALT2 |  |  | CMP0_OUT |  | DISABLED
― | J1 11 | ― | PTC6 | 63 | CMP0_IN0 | PTC6/LLWU_P10 | SPI0_MOSI | EXTRG_IN |  | SPI0_MISO |  |  | CMP0_IN0
― | J1 01 | ― | PTC7 | 64 | CMP0_IN1 | PTC7 | SPI0_MISO |  |  | SPI0_MOSI |  |  | CMP0_IN1
― | J1 14 | D6 | PTC8 | 65 | CMP0_IN2 | PTC8 | I2C0_SCL | FTM0_CH4 |  |  |  |  | CMP0_IN2
― | J1 16 | D7 | PTC9 | 66 | CMP0_IN3 | PTC9 | I2C0_SDA | FTM0_CH5 |  |  |  |  | CMP0_IN3
― | J1 13 | ― | PTC10 | 67 |  | PTC10 | I2C1_SCL |  |  |  |  |  | DISABLED
― | J1 15 | ― | PTC11 | 68 |  | PTC11 | I2C1_SDA |  |  |  |  |  | DISABLED
― | J2 01 | ― | PTC12 | 69 |  | PTC12 |  |  | FTM_CLKIN0 |  |  |  | DISABLED
― | J2 03 | ― | PTC13 | 70 |  | PTC13 |  |  | FTM_CLKIN1 |  |  |  | DISABLED
― | J2 05 | ― | PTC16 | 71 |  | PTC16 |  |  |  |  |  |  | DISABLED
― | J2 07 | ― | PTC17 | 72 |  | PTC17 |  |  |  |  |  |  | DISABLED
― | J2 06 | D10 | PTD0 | 73 |  | PTD0 | SPI0_PCS0 |  | FTM0_CH0 |  |  |  | DISABLED
Blue LED | J2 12 | D13 | PTD1 | 74 | ADC0_SE5b | PTD1 | SPI0_SCK |  | FTM0_CH1 |  |  |  | ADC0_SE5b
― | J2 08 | D11 | PTD2 | 75 |  | PTD2 | SPI0_MOSI | UART2_RX | FTM0_CH2 | SPI0_MISO |  |  | DISABLED
― | J2 10 | D12 | PTD3 | 76 |  | PTD3 | SPI0_MISO | UART2_TX | FTM0_CH3 | SPI0_MOSI |  |  | DISABLED
― | J1 06 | D2 | PTD4 | 77 |  | PTD4/LLWU_P14 | SPI1_PCS0 | UART2_RX | FTM0_CH4 |  |  |  | DISABLED
― | J2 04 | D9 | PTD5 | 78 | ADC0_SE6b | PTD5 | SPI1_SCK | UART2_TX | FTM0_CH5 |  |  |  | ADC0_SE6b
― | J2 17 | ― | PTD6 | 79 | ADC0_SE7b | PTD6/LLWU_P15 | SPI1_MOSI | UART0_RX |  | SPI1_MISO |  |  | ADC0_SE7b
― | J2 19 | ― | PTD7 | 80 |  | PTD7 | SPI1_MISO | UART0_TX |  | SPI1_MOSI |  |  | DISABLED
Power | J2 14 | GND | GND
― | J2 15 | ― | ―
― | J9 02 | RFU | SDA_PTD5
Power | J9 04 | IOREF | P3V3
Power | J9 08 | 3.3V | P3V3
Power | J9 10 | 5V | P5V_USB
Power | J9 12 | GND | GND
Power | J9 14 | GND | GND
Power | J9 16 | VIN | P5-9V_VIN
* AREF is not connected to VREFH by default. VREFH is connected to P3V3_KL25Z by default. To supply an external AREF, cut the trace SH1 and install a 0ohm resistor or a wire short on R3.
 | = valid signal options

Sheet: IO Header Pinouts
FRDM-KL25Z I/O Connector signal connections
J1 |  |  |  | J2 |  |  |  | J9 |  |  |  | J10
Pin | Signal | Pin | Signal | Pin | Signal | Pin | Signal | Pin | Signal | Pin | Signal | Pin | Signal | Pin | Signal
J1 01 | PTC7 | J1 02 | PTA1 | J2 01 | PTC12 | J2 02 | PTA13 | J9 01 | PTB8 | J9 02 | SDA_PTD5 | J10 01 | PTE20 | J10 02 | PTB0
J1 03 | PTC0 | J1 04 | PTA2 | J2 03 | PTC13 | J2 04 | PTD5 | J9 03 | PTB9 | J9 04 | P3V3 | J10 03 | PTE21 | J10 04 | PTB1
J1 05 | PTC3 | J1 06 | PTD4 | J2 05 | PTC16 | J2 06 | PTD0 | J9 05 | PTB10 | J9 06 | PTA20 | J10 05 | PTE22 | J10 06 | PTB2
J1 07 | PTC4 | J1 08 | PTA12 | J2 07 | PTC17 | J2 08 | PTD2 | J9 07 | PTB11 | J9 08 | P3V3 | J10 07 | PTE23 | J10 08 | PTB3
J1 09 | PTC5 | J1 10 | PTA4 | J2 09 | PTA16 | J2 10 | PTD3 | J9 09 | PTE2 | J9 10 | P5V_USB | J10 09 | PTE29 | J10 10 | PTC2
J1 11 | PTC6 | J1 12 | PTA5 | J2 11 | PTA17 | J2 12 | PTD1 | J9 11 | PTE3 | J9 12 | GND | J10 11 | PTE30 | J10 12 | PTC1
J1 13 | PTC10 | J1 14 | PTC8 | J2 13 | PTE31 | J2 14 | GND | J9 13 | PTE4 | J9 14 | GND
J1 15 | PTC11 | J1 16 | PTC9 | J2 15 | NC | J2 16 | VREFH | J9 15 | PTE5 | J9 16 | P5-9V_VIN
 |  |  |  | J2 17 | PTD6 | J2 18 | PTE1
 |  |  |  | J2 19 | PTD7 | J2 20 | PTE0

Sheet: R3 Compatibility
FRDM-KL25Z Arduino™ R3 pin layout compatibility comparison chart
 |  | UART | PWM | GPIO | Interrupt | I2C | SPI | A/D | Input Capture | Comparator | LED
D0 | Arduino Uno R3 | RX |  | ü | ü
 | FREEDOM-KL25Z (PTA1) | UART0_RX | FTM2_CH0 | ü | ü |  |  |  | FTM2_CH0
D1 | Arduino Uno R3 | TX |  | ü | ü
 | FREEDOM-KL25Z (PTA2) | UART0_TX | FTM2_CH1 | ü | ü |  |  |  | FTM2_CH1
D2 | Arduino Uno R3 |  |  | ü | ü
 | FREEDOM-KL25Z (PTD4) |  | FTM0_CH4 | ü | ü |  |  |  | FTM0_CH4
D3 | Arduino Uno R3 |  | ü | ü | ü
 | FREEDOM-KL25Z (PTA12) |  | FTM1_CH0 | ü | ü |  |  |  | FTM1_CH0
D4 | Arduino Uno R3 |  |  | ü | ü
 | FREEDOM-KL25Z (PTA4) |  | FTM0_CH1 | ü | ü |  |  |  | FTM0_CH1
D5 | Arduino Uno R3 |  | ü | ü | ü
 | FREEDOM-KL25Z (PTA5) |  | FTM0_CH2 | ü | ü |  |  |  | FTM0_CH2
D6 | Arduino Uno R3 |  | ü | ü | ü |  |  |  |  | ü
 | FREEDOM-KL25Z (PTC8) |  | FTM0_CH4 | ü | X | I2C0_SCL |  |  | FTM0_CH4 | COMP0_IN2
D7 | Arduino Uno R3 |  |  | ü | ü |  |  |  |  | ü
 | FREEDOM-KL25Z (PTC9) |  | FTM0_CH5 | ü | X | I2C0_SDA |  |  | FTM0_CH5 | COMP0_IN3
D8 | Arduino Uno R3 |  |  | ü | ü |  |  |  | ü
 | FREEDOM-KL25Z (PTA13) |  | FTM1_CH1 | ü | ü |  |  |  | FTM1_CH1
D9 | Arduino Uno R3 |  | ü | ü | ü
 | FREEDOM-KL25Z (PTD5) |  | FTM0_CH5 | ü | ü |  |  |  | FTM0_CH5
D10 | Arduino Uno R3 |  | ü | ü | ü |  | ü
 | FREEDOM-KL25Z (PTD0) |  | FTM0_CH0 | ü | ü |  | SPI0_PCS0 |  | FTM0_CH0
D11 | Arduino Uno R3 |  |  | ü | ü |  | ü
 | FREEDOM-KL25Z (PTD2) | UART2_RX | FTM0_CH2 | ü | ü |  | SPI0_MOSI |  | FTM0_CH2
D12 | Arduino Uno R3 |  |  | ü | ü |  | ü
 | FREEDOM-KL25Z (PTD3) | UART2_TX | FTM0_CH3 | ü | ü |  | SPI0_MISO |  | FTM0_CH3
D13 | Arduino Uno R3 |  |  | ü | ü |  | ü |  |  |  | ü
 | FREEDOM-KL25Z (PTD1) |  | FTM0_CH1 | ü | ü |  | SPI0_SCK | ADC0_SE5b | FTM0_CH1 |  | FTM0_CH1
D14 | Arduino Uno R3 |  |  | ü | ü | SDA |  | A4
 | FREEDOM-KL25Z (PTE0) |  |  | ü | X | I2C1_SDA |  | X
D15 | Arduino Uno R3 |  |  | ü | ü | SCL |  | A5
 | FREEDOM-KL25Z (PTE1) |  |  | ü | X | I2C1_SCL |  | X
A0 | Arduino Uno R3 |  |  | ü | ü |  |  | A0
 | FREEDOM-KL25Z (PTB0) |  |  | ü | X | I2C0_SCL |  | ADC0_SE8 | FTM1_CH0
A1 | Arduino Uno R3 |  |  | ü | ü |  |  | A1
 | FREEDOM-KL25Z (PTB1) |  |  | ü | X | I2C0_SDA |  | ADC0_SE9 | FTM1_CH1
A2 | Arduino Uno R3 |  |  | ü | ü |  |  | A2
 | FREEDOM-KL25Z (PTB2) |  |  | ü | X | I2C0_SCL |  | ADC0_SE12 | FTM2_CH0
A3 | Arduino Uno R3 |  |  | ü | ü |  |  | A3
 | FREEDOM-KL25Z (PTB3) |  |  | ü | X | I2C0_SDA |  | ADC0_SE13 | FTM2_CH1
A4 | Arduino Uno R3 |  |  | ü | ü | SDA |  | A4
 | FREEDOM-KL25Z (PTC2) |  |  | ü | X | I2C1_SDA |  | ADC0_SE11
A5 | Arduino Uno R3 |  |  | ü | ü | SCL |  | A5
 | FREEDOM-KL25Z (PTC1) |  |  | ü | X | I2C1_SCL |  | ADC0_SE15

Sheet: OpenSDA Pinouts
OpenSDA Pinouts
K20 32QFN | Pin Name | Use Case | DEFAULT | ALT0 | ALT1 | ALT2 | ALT3 | ALT4 | ALT5 | ALT6 | ALT7
1 | VDD | 3.3V | VDD | VDD
2 | VSS | GND | VSS | VSS
3 | USB0_DP | USB D+ | USB0_DP | USB0_DP
4 | USB0_DM | USB D- | USB0_DM | USB0_DM
5 | VOUT33 | 2.2uF to GND | VOUT33 | VOUT33
6 | VREGIN | USB VBUS (5V) | VREGIN | VREGIN
7 | VDDA | 3.3V | VDDA | VDDA
8 | VSSA | GND | VSSA | VSSA
9 | XTAL32 | No Connect - pads for XTAL available | XTAL32 | XTAL32
10 | EXTAL32 | No Connect - pads for XTAL available | EXTAL32 | EXTAL32
11 | VBAT | No Connect | VBAT | VBAT
12 | PTA0 | Debug Connector | JTAG_TCLK/SWD_CLK/EZP_CLK | TSI0_CH1 | PTA0 | UART0_CTS_b/UART0_COL_b | FTM0_CH5 |  |  |  | JTAG_TCLK/SWD_CLK
13 | PTA1 | Debug Connector | JTAG_TDI/EZP_DI | TSI0_CH2 | PTA1 | UART0_RX | FTM0_CH6 |  |  |  | JTAG_TDI
14 | PTA2 | Debug Connector | JTAG_TDO/TRACE_SWO/EZP_DO | TSI0_CH3 | PTA2 | UART0_TX | FTM0_CH7 |  |  |  | JTAG_TDO/TRACE_SWO
15 | PTA3 | Debug Connector | JTAG_TMS/SWD_DIO | TSI0_CH4 | PTA3 | UART0_RTS_b | FTM0_CH0 |  |  |  | JTAG_TMS/SWD_DIO
16 | PTA4/LLWU_P3 | SWD_EN (disconnecto SPI port from target) | NMI_b/EZP_CS_b | TSI0_CH5 | PTA4/LLWU_P3 |  | FTM0_CH1 |  |  |  | NMI_b
17 | PTA18 | 8MHz resonator | EXTAL0 | EXTAL0 | PTA18 |  | FTM0_FLT2 | FTM_CLKIN0
18 | PTA19 | 8MHz resonator | XTAL0 | XTAL0 | PTA19 |  | FTM1_FLT0 | FTM_CLKIN1 |  | LPTMR0_ALT1
19 | RESET_b | Voltage divider to USB VBUS | RESET_b | RESET_b
20 | PTB0/LLWU_P5 | SWD_OE (Output Buffer Enable) | ADC0_SE8/TSI0_CH0 | ADC0_SE8/TSI0_CH0 | PTB0/LLWU_P5 | I2C0_SCL | FTM1_CH0 |  |  | FTM1_QD_PHA
21 | PTB1 | RESET Output to target MCU | ADC0_SE9/TSI0_CH6 | ADC0_SE9/TSI0_CH6 | PTB1 | I2C0_SDA | FTM1_CH1 |  |  | FTM1_QD_PHB
22 | PTC1/LLWU_P6 | SPI Flash Reset | ADC0_SE15/TSI0_CH14 | ADC0_SE15/TSI0_CH14 | PTC1/LLWU_P6 | SPI0_PCS3 | UART1_RTS_b | FTM0_CH0 |  | I2S0_TXD0
23 | PTC2 | SPI Flash CS | ADC0_SE4b/CMP1_IN0/TSI0_CH15 | ADC0_SE4b/CMP1_IN0/TSI0_CH15 | PTC2 | SPI0_PCS2 | UART1_CTS_b | FTM0_CH1 |  | I2S0_TX_FS
24 | PTC3/LLWU_P7 | Connect to target MCU TX pin | CMP1_IN1 | CMP1_IN1 | PTC3/LLWU_P7 | SPI0_PCS1 | UART1_RX | FTM0_CH2 | CLKOUT | I2S0_TX_BCLK
25 | PTC4/LLWU_P8 | Connect to target MCU RX pin | DISABLED |  | PTC4/LLWU_P8 | SPI0_PCS0 | UART1_TX | FTM0_CH3 |  | CMP1_OUT
26 | PTC5/LLWU_P9 | SWD_CLK to target MCU, SPI to SPI Flash | DISABLED |  | PTC5/LLWU_P9 | SPI0_SCK | LPTMR0_ALT2 | I2S0_RXD0 |  | CMP0_OUT
27 | PTC6/LLWU_P10 | SWD_DIO to 74*126, SPI to SPI Flash | CMP0_IN0 | CMP0_IN0 | PTC6/LLWU_P10 | SPI0_SOUT | PDB0_EXTRG | I2S0_RX_BCLK |  | I2S0_MCLK
28 | PTC7 | SWD_DIO to target MCU, SPI Flash | CMP0_IN1 | CMP0_IN1 | PTC7 | SPI0_SIN | USB_SOF_OUT | I2S0_RX_FS
29 | PTD4/LLWU_P14 | Green LED (may no-pop) | DISABLED |  | PTD4/LLWU_P14 | SPI0_PCS1 | UART0_RTS_b | FTM0_CH4 |  | EWM_IN
30 | PTD5 | Special case -- connected to IO header | ADC0_SE6b | ADC0_SE6b | PTD5 | SPI0_PCS2 | UART0_CTS_b/UART0_COL_b | FTM0_CH5 |  | EWM_OUT_b
31 | PTD6/LLWU_P15 | Special case -- connected to RTC_CLKIN | ADC0_SE7b | ADC0_SE7b | PTD6/LLWU_P15 | SPI0_PCS3 | UART0_RX | FTM0_CH6 |  | FTM0_FLT0
32 | PTD7 | USB 5V Power Sense | DISABLED |  | PTD7 | CMT_IRO | UART0_TX | FTM0_CH7 |  | FTM0_FLT1

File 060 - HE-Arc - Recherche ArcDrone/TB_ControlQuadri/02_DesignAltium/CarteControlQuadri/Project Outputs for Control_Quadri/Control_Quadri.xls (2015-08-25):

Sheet: BOM Report
Bill of Materials |  |  | Bill of Materials For Project [Control_Quadri.PrjPCB] (No PCB Document Selected)
Source Data From: |  | Control_Quadri.PrjPCB
Project: |  | Control_Quadri.PrjPCB
Variant: |  | None
Creation Date: | 04.06.2012 | 13:27:51
Print Date: | 41064 | 41064.56105
Footprint | Comment | LibRef | Designator | Description | Quantity
080501 | 4.7uF | CAPA | C1 |  | 1
080501 | 20 pF | CAPA | C1, C2 |  | 2
120601 | 0.22 uF | CAPA | C2 |  | 1
080501 | 10 uF | CAPA | C3, C5, C9 |  | 3
120601 | 100 nF | CAPA | C4, C6 |  | 2
080501 | 10 nF | CAPA | C7 |  | 1
060301 | 470 nF | CAPA | C8 |  | 1
080501 | 22 uF | CAPA | C10 |  | 1
XT-5 | 32kHz | CRYSTAL | G1 |  | 1
Crystal | CRYSTAL | CRYSTAL | G2 |  | 1
080503 | 2.2 uH | INDUCTOR | L1 |  | 1
060301_led |  | LED | LED1 |  | 1
080501 | 10k | RES | R1, R2, R3, R4, R5 |  | 5
080501 | 820 Ohm | RES | R6, R11, R12, R13, R14 |  | 5
080501 | 1.6 kOhm | RES | R7, R8, R9, R10, R17 |  | 5
080501 | 8.2 kOhm | RES | R16 |  | 1
080501 | 100 kOhm | RES | R18 |  | 1
 | DC/DC | TPS62160 | U1 | TPS62162 | 1
QFP100-1 | MK10 | MK10 | U1 |  | 1
MS5534B | MS5534_CM | MS5534B | U2 | Barometer Module | 1
LGA-14L | LSM303DLHC | LSM303DLHC | U3 | Accéléromètre et magnétomètre | 1
LGA-16 | L3G4200D | L3G4200D | U4 | Gyroscope | 1
XBee-Pro | MaxStream XBee-PRO | MaxStream XBee-PRO | U5 |  | 1
 | LineDriver | LineDriver | U6 |  | 1
SOIC127P1030-16M | MIC4468 | MIC4468 | U7 |  | 1
SOT26A-6AM | Max4173 | Max4173 | U8 | ificateur capteur de courant | 1
J2X3_2.54 | CON6/CP | CON6/CP | X1, X2, X3, X4 | Connecteur contrôleur moteurs 1 (avant) & 2 (droite), Connecteur contrôleur moteurs 3 (arrière) & 4 (gauche), Connecteur récepteur télécommande cannaux 1 & 2, Connecteur récepteur télécommande cannaux 3 & 4 | 4
 |  |  |  |  | 46
Approved |  | Notes

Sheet: Project Information
Project Full Path | P:\Formation\010-Bachelor\040-TravailBachelor\GEL\12GEL-TB205-ControlQuadri\010-Etudiants\02_DesignAltium\Control_Quadri.PrjPCB
Project Filename | Control_Quadri.PrjPCB
Variant Name | None
Data-Source Filename | Control_Quadri.PrjPCB
Data-Source Full Path | P:\Formation\010-Bachelor\040-TravailBachelor\GEL\12GEL-TB205-ControlQuadri\010-Etudiants\02_DesignAltium\Control_Quadri.PrjPCB
Title | Bill of Materials For Project [Control_Quadri.PrjPCB] (No PCB Document Selected)
Total Quantity | 46
Report Time | 13:27:51
Report Date | 04.06.2012
Report Date & Tine | 04.06.2012 13:27:51
Output Name | Bill of Materials
Output Type | BOM_PartType
Output Generator Name | BOM
Output Generator Description | Bill of Materials

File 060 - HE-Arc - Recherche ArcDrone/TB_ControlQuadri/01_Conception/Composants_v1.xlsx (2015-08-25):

Référence | Article | Désignation | Technologie | Tension | Courant | Puissance | Précision | Fabricant | Référence | Fournisseur | Référence | Document | Boîtier | Prix
schéma |  |  |  | (V) | (A) | (W) | (%) |  | fabricant |  | fournisseur | pdf |  | 1 | 10
Composants passifs
C1 | Capacité 4.7 uF | C0805C475K4PACTU |  | 16 |  |  | 10 | Kemet (http://digikey.com/Suppliers/us/Kemet.page?lang=EN) | C0805C475K4PACTU | Digi-Key | C0805C475K4PACTU-ND | Ceramic Chip Capacitors (http://media.digikey.com/pdf/Data%20Sheets/Kemet%20PDFs/Ceramic%20Chip%20Caps.pdf) | 0805 | 0.0389 | 0.0389
C2 | Capacité 0.22 uF | EMK107B7224KA-T |  | 16 |  |  | 10 | Taiyo Yuden (http://digikey.com/Suppliers/us/Taiyo-Yuden.page?lang=EN) | EMK107B7224KA-T | Digi-Key | 587-1249-1-ND | EMK107B7224KA-T (http://www.yuden.co.jp/or/product/category/capacitor/EMK107B7224KA-T.pdf) | 0603 | 0.1 | 0.048
C3 | Capacité 10 uF | 08056D106KAT2A |  | 6.3 |  |  | 10 | AVX Corporation (http://digikey.com/Suppliers/us/AVX.page?lang=EN) | 08056D106KAT2A | Digi-Key | 478-1417-1-ND | X5R Dielectric (http://www.avx.com/docs/Catalogs/cx5r.pdf) | 0805 | 0.24 | 0.2
C4 | Capacité 100 nF | GRM31C5C1E104JA01L |  | 25 |  |  | 5 | Murata Electronics North America (http://digikey.com/Suppliers/us/Murata-Electronics.page?lang=EN) | GRM31C5C1E104JA01L | Digi-Key | 490-1767-2-ND | GRM31C5C1E104JA01 (http://search.murata.co.jp/Ceramy/image/img/PDF/ENG/GRM31C5C1E104JA01.pdf) | 1206 | 0.115 | 0.1
R1 | Résistance 10 kOhm | ERJ-6GEYJ103V |  |  |  | 0.125 | 5 | Panasonic - ECG (http://digikey.com/Suppliers/us/Panasonic-Electronic-Components.page?lang=EN) | ERJ-6GEYJ103V | Digi-Key | P10KACT-ND | ERJ-6GEYJ103V View All Specifications (http://industrial.panasonic.com/www-cgi/jvcr13pz.cgi?E+PZ+3+AOA0001+ERJ6GEYJ103V+7+WW) | 0805 | 0.1 | 0.0162
R2 | Résistance 10 kOhm | ERJ-6GEYJ103V |  |  |  | 0.125 | 5 | Panasonic - ECG (http://digikey.com/Suppliers/us/Panasonic-Electronic-Components.page?lang=EN) | ERJ-6GEYJ103V | Digi-Key | P10KACT-ND | ERJ-6GEYJ103V View All Specifications (http://industrial.panasonic.com/www-cgi/jvcr13pz.cgi?E+PZ+3+AOA0001+ERJ6GEYJ103V+7+WW) | 0805 | 0.1 | 0.0162
R3 | Résistance 10 kOhm | ERJ-6GEYJ103V |  |  |  | 0.125 | 5 | Panasonic - ECG (http://digikey.com/Suppliers/us/Panasonic-Electronic-Components.page?lang=EN) | ERJ-6GEYJ103V | Digi-Key | P10KACT-ND | ERJ-6GEYJ103V View All Specifications (http://industrial.panasonic.com/www-cgi/jvcr13pz.cgi?E+PZ+3+AOA0001+ERJ6GEYJ103V+7+WW) | 0805 | 0.1 | 0.0162
R4 | Résistance 10 kOhm | ERJ-6GEYJ103V |  |  |  | 0.125 | 5 | Panasonic - ECG (http://digikey.com/Suppliers/us/Panasonic-Electronic-Components.page?lang=EN) | ERJ-6GEYJ103V | Digi-Key | P10KACT-ND | ERJ-6GEYJ103V View All Specifications (http://industrial.panasonic.com/www-cgi/jvcr13pz.cgi?E+PZ+3+AOA0001+ERJ6GEYJ103V+7+WW) | 0805 | 0.1 | 0.0162
R5 | Résistance 10 kOhm | ERJ-6GEYJ103V |  |  |  | 0.125 | 5 | Panasonic - ECG (http://digikey.com/Suppliers/us/Panasonic-Electronic-Components.page?lang=EN) | ERJ-6GEYJ103V | Digi-Key | P10KACT-ND | ERJ-6GEYJ103V View All Specifications (http://industrial.panasonic.com/www-cgi/jvcr13pz.cgi?E+PZ+3+AOA0001+ERJ6GEYJ103V+7+WW) | 0805 | 0.1 | 0.0162
C5 | Capacité 10 uF | 08056D106KAT2A |  | 6.3 |  |  | 10 | AVX Corporation (http://digikey.com/Suppliers/us/AVX.page?lang=EN) | 08056D106KAT2A | Digi-Key | 478-1417-1-ND | X5R Dielectric (http://www.avx.com/docs/Catalogs/cx5r.pdf) | 0805 | 0.24 | 0.2
C6 | Capacité 100 nF | GRM31C5C1E104JA01L |  | 25 |  |  | 5 | Murata Electronics North America (http://digikey.com/Suppliers/us/Murata-Electronics.page?lang=EN) | GRM31C5C1E104JA01L | Digi-Key | 490-1767-2-ND | GRM31C5C1E104JA01 (http://search.murata.co.jp/Ceramy/image/img/PDF/ENG/GRM31C5C1E104JA01.pdf) | 1206 | 0.115 | 0.1
C7 | Capacité 10 nF | C0805C103K4RACTU |  | 16 |  |  | 10 | Kemet (http://digikey.com/Suppliers/us/Kemet.page?lang=EN) | C0805C103K4RACTU | Digi-Key | C0805C103K4RACTU-ND | Ceramic Chip (http://www.kemet.com/datasheets&C0805C103K4RACTU) | 0805 | 0.04625 | 0.04625
C8 | Capacité 470 nF | EMK107B7474KA-T |  | 16 |  |  | 10 | Taiyo Yuden (http://digikey.com/Suppliers/us/Taiyo-Yuden.page?lang=EN) | EMK107B7474KA-T | Digi-Key | 587-1250-1-ND | EMK107B7474KA-T (http://www.yuden.co.jp/or/product/category/capacitor/EMK107B7474KA-T.pdf) | 0603 | 0.1 | 0.066
R6 | Résistance 820 Ohm | RMCF0805JT820R |  |  |  | 0.125 | 5 | Stackpole Electronics Inc (http://digikey.com/Suppliers/us/Stackpole-Electronics.page?lang=EN) | RMCF0805JT820R | Digi-Key | RMCF0805JT820RCT-ND | RMCF,RMCP Series (http://www.seielect.com/Catalog/SEI-RMCF_RMCP.pdf) | 0805 | 0.03 | 0.021
R7 | Résistance 1.6k Ohm | ERJ-6GEYJ162V |  |  |  | 0.125 | 5 | Panasonic - ECG (http://digikey.com/Suppliers/us/Panasonic-Electronic-Components.page?lang=EN) | ERJ-6GEYJ162V | Digi-Key | P1.6KACT-ND | ERJ-6GEYJ162V View All Specifications (http://industrial.panasonic.com/www-cgi/jvcr13pz.cgi?E+PZ+3+AOA0001+ERJ6GEYJ162V+7+WW) | 0805 | 0.1 | 0.0162
R8 | Résistance 1.6k Ohm | ERJ-6GEYJ162V |  |  |  | 0.125 | 5 | Panasonic - ECG (http://digikey.com/Suppliers/us/Panasonic-Electronic-Components.page?lang=EN) | ERJ-6GEYJ162V | Digi-Key | P1.6KACT-ND | ERJ-6GEYJ162V View All Specifications (http://industrial.panasonic.com/www-cgi/jvcr13pz.cgi?E+PZ+3+AOA0001+ERJ6GEYJ162V+7+WW) | 0805 | 0.1 | 0.0162
R9 | Résistance 1.6k Ohm | ERJ-6GEYJ162V |  |  |  | 0.125 | 5 | Panasonic - ECG (http://digikey.com/Suppliers/us/Panasonic-Electronic-Components.page?lang=EN) | ERJ-6GEYJ162V | Digi-Key | P1.6KACT-ND | ERJ-6GEYJ162V View All Specifications (http://industrial.panasonic.com/www-cgi/jvcr13pz.cgi?E+PZ+3+AOA0001+ERJ6GEYJ162V+7+WW) | 0805 | 0.1 | 0.0162
R10 | Résistance 1.6k Ohm | ERJ-6GEYJ162V |  |  |  | 0.125 | 5 | Panasonic - ECG (http://digikey.com/Suppliers/us/Panasonic-Electronic-Components.page?lang=EN) | ERJ-6GEYJ162V | Digi-Key | P1.6KACT-ND | ERJ-6GEYJ162V View All Specifications (http://industrial.panasonic.com/www-cgi/jvcr13pz.cgi?E+PZ+3+AOA0001+ERJ6GEYJ162V+7+WW) | 0805 | 0.1 | 0.0162
R11 | Résistance 820 Ohm | RMCF0805JT820R |  |  |  | 0.125 | 5 | Stackpole Electronics Inc (http://digikey.com/Suppliers/us/Stackpole-Electronics.page?lang=EN) | RMCF0805JT820R | Digi-Key | RMCF0805JT820RCT-ND | RMCF,RMCP Series (http://www.seielect.com/Catalog/SEI-RMCF_RMCP.pdf) | 0805 | 0.03 | 0.021
R12 | Résistance 820 Ohm | RMCF0805JT820R |  |  |  | 0.125 | 5 | Stackpole Electronics Inc (http://digikey.com/Suppliers/us/Stackpole-Electronics.page?lang=EN) | RMCF0805JT820R | Digi-Key | RMCF0805JT820RCT-ND | RMCF,RMCP Series (http://www.seielect.com/Catalog/SEI-RMCF_RMCP.pdf) | 0805 | 0.03 | 0.021
R13 | Résistance 820 Ohm | RMCF0805JT820R |  |  |  | 0.125 | 5 | Stackpole Electronics Inc (http://digikey.com/Suppliers/us/Stackpole-Electronics.page?lang=EN) | RMCF0805JT820R | Digi-Key | RMCF0805JT820RCT-ND | RMCF,RMCP Series (http://www.seielect.com/Catalog/SEI-RMCF_RMCP.pdf) | 0805 | 0.03 | 0.021
R14 | Résistance 820 Ohm | RMCF0805JT820R |  |  |  | 0.125 | 5 | Stackpole Electronics Inc (http://digikey.com/Suppliers/us/Stackpole-Electronics.page?lang=EN) | RMCF0805JT820R | Digi-Key | RMCF0805JT820RCT-ND | RMCF,RMCP Series (http://www.seielect.com/Catalog/SEI-RMCF_RMCP.pdf) | 0805 | 0.03 | 0.021
R15 | Résistance 0.003 Ohm | WSLP59313L000FEB (http://www.digikey.com/product-detail/en/WSLP59313L000FEB) |  |  |  | 7 | 1 | Vishay Dale (http://digikey.com/Suppliers/us/Vishay-Dale.page?lang=EN) | WSLP59313L000FEB | Digi-Key | WSLPD-.003CT-ND | WSLP3921,3931 (http://www.vishay.com/docs/30176/wslp3921.pdf) | 15078 | 4.42 | 3.757
R16 | Réistance 8.2 kOhm | ERJ-6GEYJ822V (http://www.digikey.com/product-detail/en/ERJ-6GEYJ822V) |  |  |  | 0.125 | 5 | Panasonic - ECG (http://digikey.com/Suppliers/us/Panasonic-Electronic-Components.page?lang=EN) | ERJ-6GEYJ822V (http://www.digikey.com/product-detail/en/ERJ-6GEYJ822V) | Digi-Key | P8.2KACT-ND | ERJ-6GEYJ822V View All Specifications (http://industrial.panasonic.com/www-cgi/jvcr13pz.cgi?E+PZ+3+AOA0001+ERJ6GEYJ822V+7+WW) | 0805 | 0.1 | 0.0162
R17 | Résistance 1.6k Ohm | ERJ-6GEYJ162V |  |  |  | 0.125 | 5 | Panasonic - ECG (http://digikey.com/Suppliers/us/Panasonic-Electronic-Components.page?lang=EN) | ERJ-6GEYJ162V | Digi-Key | P1.6KACT-ND | ERJ-6GEYJ162V View All Specifications (http://industrial.panasonic.com/www-cgi/jvcr13pz.cgi?E+PZ+3+AOA0001+ERJ6GEYJ162V+7+WW) | 0805 | 0.1 | 0.0162
C9 | Capacité 10 uF | GRM21BR61E106KA73L (http://www.digikey.com/product-detail/en/GRM21BR61E106KA73L) |  | 25 |  |  | 10 | Murata Electronics North America (http://digikey.com/Suppliers/us/Murata-Electronics.page?lang=EN) | GRM21BR61E106KA73L (http://www.digikey.com/product-detail/en/GRM21BR61E106KA73L) | Digi-Key | 490-5523-1-ND | Chip Monolithic Ceramic Caps Catalog (http://www.murata.com/products/catalog/pdf/c02e.pdf) | 0805 | 0.26 | 0.231
C10 | Capacité 22uF | C2012X5R1A226M/1.25 (http://www.digikey.com/product-detail/en/C2012X5R1A226M%2F1.25) |  | 10 |  |  |  | TDK Corporation (http://digikey.com/Suppliers/us/TDK.page?lang=EN) | C2012X5R1A226M/1.25 (http://www.digikey.com/product-detail/en/C2012X5R1A226M%2F1.25) | Digi-Key | 445-7665-1-ND | C Series General App (http://www.tdk.com/pdf/general_B11.pdf) | 0805 | 0.52 | 0.455
R18 | Résistance 100 k Ohm | ERJ-6GEYJ104V (http://www.digikey.com/product-detail/en/ERJ-6GEYJ104V) |  |  |  | 0.125 | 5 | Panasonic - ECG (http://digikey.com/Suppliers/us/Panasonic-Electronic-Components.page?lang=EN) | ERJ-6GEYJ104V (http://www.digikey.com/product-detail/en/ERJ-6GEYJ104V) | Digi-Key | P100KACT-ND | ERJ-6GEYJ104V View All Specifications (http://industrial.panasonic.com/www-cgi/jvcr13pz.cgi?E+PZ+3+AOA0001+ERJ6GEYJ104V+7+WW) | 0805 | 0.1 | 0.0162
L1 | Inductance 2.2 uH | BRC2012T2R2MD (http://www.digikey.com/product-detail/en/BRC2012T2R2MD) |  |  |  |  | 20 | Taiyo Yuden | BRC2012T2R2MD (http://www.digikey.com/product-detail/en/BRC2012T2R2MD) | Digi-Key | 587-2905-1-ND | BR Series (http://www.yuden.co.jp/ut/product/pdf/wound07_e.pdf) | 0805 | 0.28 | 0.268
G1 | Crystal 32.768 kHz | ECS-.327-12.5-38 (http://www.digikey.com/product-detail/en/ECS-.327-12.5-38) |  |  |  |  |  | ECS Inc (http://digikey.com/Suppliers/us/ECS.page?lang=EN) | ECS-.327-12.5-38 (http://www.digikey.com/product-detail/en/ECS-.327-12.5-38) | Digi-Key | XC1616CT-ND | ECX-71 (http://www.ecsxtal.com/store/pdf/ecx-71.pdf) | Flat leads | 1.13 | 0.975
G2
 |  |  |  |  |  |  |  |  |  |  |  | Prix partiel |  | 1.99 | 1.01
Semiconducteurs discrets
LED1 | Led verte | LG L29K-G2J1-24-Z |  | 1.7 | 0.002 |  |  | OSRAM Opto Semiconductors Inc (http://digikey.com/Suppliers/us/Osram.page?lang=EN) | LG L29K-G2J1-24-Z | Digi-Key | 475-2709-1-ND | LG L29K | 603 | 0.16 | 0.137
 |  |  |  |  |  |  |  |  |  |  |  | Prix partiel |  | 0.16 | 0.14
Circuits intégrés
U1 | Alimentation DC/DC | TPS62160DGKT |  |  | 1 |  |  | Texas Instruments (http://digikey.com/Suppliers/us/Diodes.page?lang=EN) | TPS62160DGKT (http://www.digikey.com/product-detail/en/TPS62160DGKT) | Digi-Key | 296-30318-1-ND | TPS6216x Family (http://www.ti.com/lit/ds/symlink/tps62160.pdf) | MSOP-8 | 3.89 | 3.48
U3 | Accéléromètre/Magnétomètre | LSM303DLHCTR |  | 3.3 | 0.00011 |  |  | STMicroelectronics (http://digikey.com/Suppliers/us/STMicroelectronics.page?lang=EN) | LSM303DLHCTR | Digi-Key | 497-11918-1-ND | LSM303DLHC Preliminary (http://www.st.com/internet/com/TECHNICAL_RESOURCES/TECHNICAL_LITERATURE/DATASHEET/DM00027543.pdf) | LGA-14 | 8.20 | 7.37
U4 | Gyroscope | L3G4200DTR |  | 3.3 | 0.0061 |  |  | STMicroelectronics (http://digikey.com/Suppliers/us/STMicroelectronics.page?lang=EN) | L3G4200DTR | Digi-Key | 497-11071-1-ND | L3G4200D (http://www.st.com/internet/com/TECHNICAL_RESOURCES/TECHNICAL_LITERATURE/DATASHEET/CD00265057.pdf) | LGA-16 | 12.61 | 11.33
U5 | Module de communication RF | XBP24BZ7WIT-004J |  | 3.3 | 0.205 |  |  | Digi International (http://www2.mouser.com/digi/) | XBP24BZ7WIT-004J | Mouser | 888-XBP24BZ7WIT-004J | http://ftp1.digi.com/support/documentation/90000976_K.pdf | --- | 29.57 | 29.57
U6 | Line driver | 74VHC125D,118 |  | 3.3 | 0.025 |  |  | NXP Semiconductors (http://digikey.com/Suppliers/us/NXP-Semiconductors.page?lang=EN) | 74VHC125D,118 | Digi-Key | 568-5167-1-ND | 74VHC(T)125 (http://www.nxp.com/documents/data_sheet/74VHC_VHCT125.pdf) | SOIC-14 | 0.68 | 0.577
U7 | Driver mosfet | MIC4468ZWM | 1.6kOhm | 3.3 |  |  |  | Micrel Inc (http://digikey.com/Suppliers/us/Micrel.page?lang=EN) | MIC4468ZWM | Digi-Key | 576-1213-ND | MIC4467, MIC4468, MIC4469 (http://www.micrel.com/_PDF/mic4467.pdf) | SOIC-16 | 4.01 | 3.2
U8 | Amplificateur capteur de courrant | MAX4173TEUT+T (http://www.digikey.com/product-detail/en/MAX4173TEUT%2BT) |  | 3.3 | 0.001 |  |  | Maxim Integrated Products (http://digikey.com/Suppliers/us/Maxim.page?lang=EN) | MAX4173TEUT+T (http://www.digikey.com/product-detail/en/MAX4173TEUT%2BT) | Digi-Key | MAX4173TEUT+TCT-ND | MAX4173T/F/H (http://datasheets.maxim-ic.com/en/ds/MAX4173-MAX4173T.pdf) | SOT-23 | 2.9 | 2.1852
--- | Starter kit maxstream | XBP24-DKS |  |  |  |  |  | Digi International/Maxstream (http://digikey.com/Suppliers/us/Digi-International-MaxStream.page?lang=EN) | XBP24-DKS | Digi-Key | XBP24-DKS-ND | http://ftp1.digi.com/support/documentation/90000976_K.pdf | --- | 179 | 179
 | connecteurs femelle | 141488 |  |  |  |  |  | distrelec | 141488
 |  |  |  |  |  |  |  |  |  |  |  | Prix partiel |  | 240.86 | 236.72
Electromécanique
U2 | Capteur de pression et de température | MS5534-CM |  | 3.3 | 0.001 |  |  | Measurement Specialties Inc. (http://digikey.com/Suppliers/us/Measurement-Specialties.page?lang=EN) | MS5534-CM | Digi-Key | 223-1100-2-ND | MS5534-CM (http://media.digikey.com/pdf/Data%20Sheets/Measurement%20Specialties%20PDFs/MS5534-CM.pdf) | --- | 17.66 | 17.66
 |  |  |  |  |  |  |  |  |  |  |  | Prix partiel |  | 17.66 | 17.66
PCB
 |  |  |  |  |  |  |  |  |  |  |  |  |  | 0.00 | 0.00
 |  |  |  |  |  |  |  |  |  |  |  | Prix partiel |  | 0.00 | 0.00
 |  |  |  |  |  |  |  |  |  |  | Prix totaux |  |  | 260.67 | 255.52 | Attention USD

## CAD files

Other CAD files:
060 - HE-Arc - Recherche ArcDrone/RevisionSoftwareQuadri/Jacot-Schnegg/Software/Sources/Workspace/SoftQuadriCoptere/MK10DN512Z_INTERNAL_RAM/Sources/Gestionnaires/main.obj
060 - HE-Arc - Recherche ArcDrone/RevisionSoftwareQuadri/Jacot-Schnegg/Software/Sources/Workspace/SoftQuadriCoptere/MK10DN512Z_INTERNAL_FLASH/Sources/Gestionnaires/main.obj
060 - HE-Arc - Recherche ArcDrone/RevisionSoftwareQuadri/Jacot-Schnegg/Software/Sources/Workspace/SoftQuadriCoptere/MK10DN512Z_INTERNAL_FLASH/Project_Settings/Startup_Code/kinetis_sysinit.obj
060 - HE-Arc - Recherche ArcDrone/RevisionSoftwareQuadri/Jacot-Schnegg/Software/Sources/Workspace/SoftQuadriCoptere/MK10DN512Z_INTERNAL_FLASH/Sources/Gestionnaires/gLabview.obj
060 - HE-Arc - Recherche ArcDrone/RevisionSoftwareQuadri/Jacot-Schnegg/Software/Sources/Workspace/SoftQuadriCoptere/MK10DN512Z_INTERNAL_FLASH/Sources/Interfaces/iFlextimer.obj
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

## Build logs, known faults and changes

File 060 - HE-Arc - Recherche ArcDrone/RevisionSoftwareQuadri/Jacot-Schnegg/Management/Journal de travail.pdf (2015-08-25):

Prise en main

dimanche 21 octobre 2012
13:05

Journal de travail Page 1

A faire

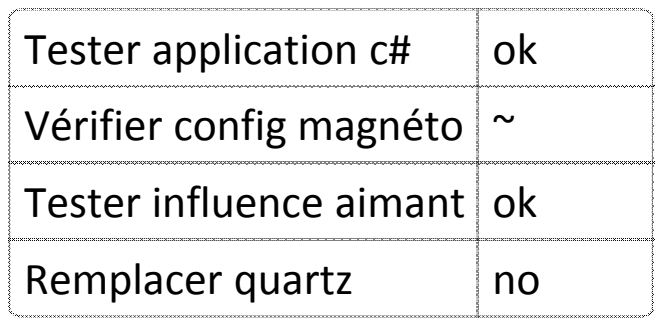
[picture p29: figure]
Tester application c#; Vérifier config magnéto ~; Tester influence aimant ok; Remplacer quartz

Constatation

Si la carte ne bouge pas, on constate des pics sur le graphe de l'accéléromètre. Cela est dû on fait que le capteur envoi la valeur en signé mais tous le traitement sur la carte et dans le soft c# est fait avec des variables non signée. La valeur variant autour de zero, il arrive qu'elle soit négative. En non signé, un nombre signé à une grande valeur.

La lecture du magnétomètre fonctionne une fois. Il semble que le bit lock ne se reset pas. Il faut essayer de faire la lecture des trois axe à la suite et non pas un après l'autre.

Favre à cru avoir régler le gain du magnéto sur 1100 alors qu'il est en fait sur 230. Nous avons conserver se réglage afin d'avoir une plage de réglage de +‐ 8.1 gauss

dimanche 21 octobre 2012
13:19

A faire

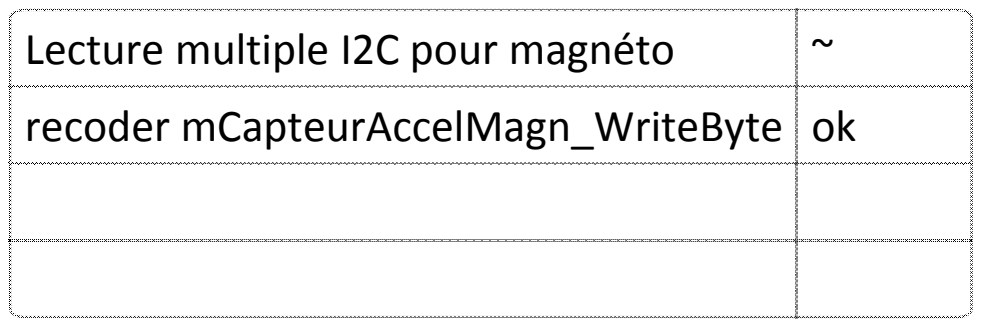
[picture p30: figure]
Lecture multiple I2C pour magnéto; recoder mCapteurAccelMagn_WriteByte ok

Constatation

Avec l'aide de M. Monnerat, on s'est aperçu que la séquence de lecture de l'i2c était fausse. Il faut l'a recoder.

Procédure pour lecture multiple:
Activer ack auto
Lire 5 byte
Désactiver ack auto
Lire le 6ème byte

L'i2c à une fréqunce de 208 kHz, c'est pas ce qu'on devrait avoir avec la config de Favre. A vérifier. Il faudrait une fréquence de 100 MHz

La fonction mCapteurAccelMagn_WriteByte n'était pas juste, elle a été corrigée. Il fallait tester si le bus est busy au début et tester le ack après chaque wait.

dimanche 21 octobre 2012
13:20

A faire

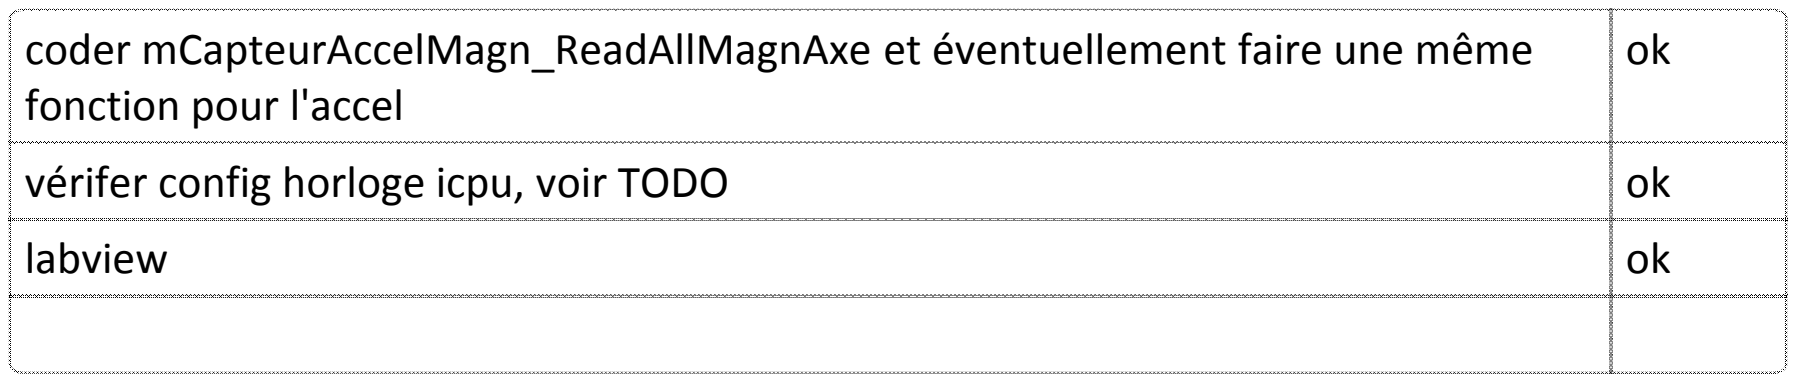
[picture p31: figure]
fonction pour l'accel; labview

coder mCapteurAccelMagn_ReadAllMagnAxe et éventuellement faire une même

vérifer config horloge icpu, voir TODO | ok

Constatation

Labview:
Modification de la trame, suppression du type.

La vérification de la configuration de l'horloge n'a rien decelée d'anormal. La mesure à l'oscillo donne toujours 208 kHz.

Après avoir codé la lecture multiple, on constate que la lecture ne marche pas, on reçois toujours la même valeur même au démarrage du programme. Sur l'oscillo on voit qu'une donnée passée, il doit y avoir un problème dans la fonction de lecture multiple.

Après discussion avec M. Berly, abandonner le magnéto et vérifier les valeurs de l'accéléromètre et du gyro.

dimanche 21 octobre 2012
13:20

A faire

vérifier les valeur renvoyer par le gyro ok vérifier les valeur renvoyer par l'accel ok
changer trame | ok
adapter labview | ok
test pression +temp | ok

Constatation

Changement du format de la trame envoyée par la carte: typedef enum

kDestAccel = 'B',
kDestGyro = 'C',
kDestPression = 'D',
kDestTemperature = 'E',
kDestMagn = 'F',
kDestAltitude = 'G',
kTensionAccu='H',
kCourantAccu='I',
kDutyPwm='J',

{

}kTrameDestEnum;

Les valeurs des 3 axes sont envoyées d'un coup, séparée par |

Range de mesure de l'accélération +‐ 2g codé sur 16 bits donc 1 g donne une valeur de 16384

Le gyro à un null offset qu'il faudra éliminer.

La mesure de tension fonctionne, il faut juste la transmettre en float. Pression ok temp pas testée. courant non plus

Contacter M. Pretre lorsque on a des données exploitable. Simulink dispo pour l'algorithme.

Il a trouvé un algo qui peut être implémenter sur dspic, il faut trouver un équivalent k10 arm

Il faudra ajouter le type dans la trame car la tension, le courant est donnée en float

lundi 22 octobre 2012
11:47

A faire

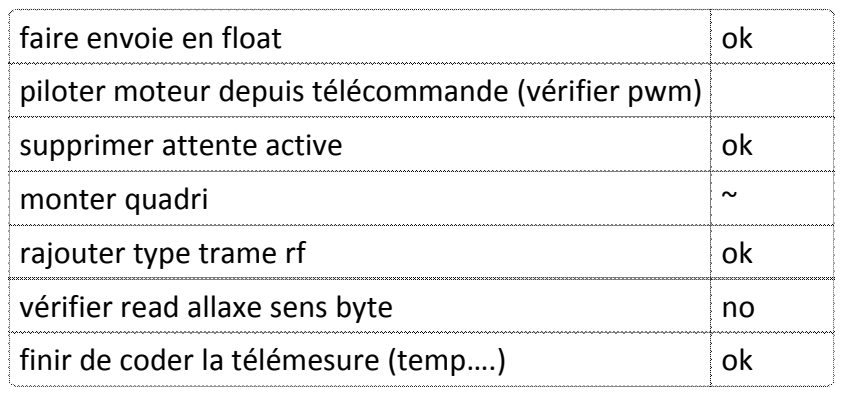
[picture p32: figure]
faire envoie en float; supprimer attente active; monter quadri; rajouter type trame rf; vérifier read allaxe sens byte

piloter moteur depuis télécommande (vérifier pwm)

finir de coder la télémesure (temp….) | ok

Constatation

Soudage des cosses sur les controleurs moteurs commande connecteur pour batterie

Si le code de lecture multiple est fonctionnel, on peut le porter pour le gyro

Capteur de pression et temp non fonctionnel

Lecture multiple non fonctionnel

Valeur bizarre pour le courant

Faut‐il transmettre la pression ou l'altitude ?

lundi 29 octobre 2012
11:36

A faire

finir monter quadri | ok
test avec télécommande | no
capteur pression temp courant ok
commande connecteur | ok

Constatation

Nous n'avons pas reçu le connecteur. On a utilisé des fiches bananes à la place.

Avant de tester avec les moteurs, nous avons vérifier les signaux PWM avec l'oscillo.

Nous avons constater une instabilité dans le signal générer par la carte. Nous pensons que le calcul du temps se fait au mauvais moment. On a essayer de le faire au flanc descendant mais sans succès.

Brancher les moteurs sur connecteur board ? Chargeur batterie

lundi 5 novembre 2012
12:25

A faire

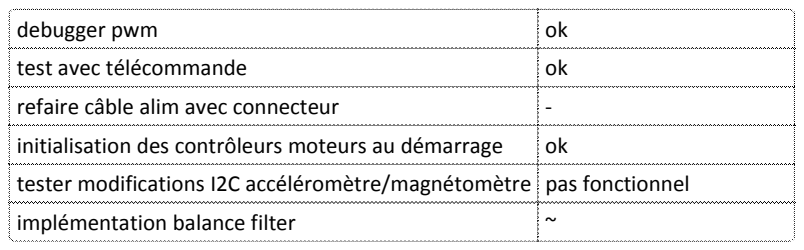
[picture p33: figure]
debugger pwm; test avec télécommande; refaire câble alim avec connecteur; implémentation balance filter

initialisation des contrôleurs moteurs au démarrage ok
tester modifications I2C accéléromètre/magnétomètre pas fonctionnel

Constatation

Correction erreur soustraction calcul duty cycle

Prévoir initialisation des contrôleurs moteurs au démarrage

Si les modifications I2C fonctionnent pour l'accéléromètre et le magnétomètre, il faudrait faire les mêmes pour le gyroscope (lecture multiple et enlever boucle d'attente…)

Bug qu'il y avait encore :
‐ lecture dans le vide avant de lire n bytes (sinon valeur rien à voir)
‐ registre decalé de 1 pour l'accéléromètre
‐ gain trop petit pour le magnétomètre
‐ envoi i2c faux : LSB modifié avant envoi donc on n'écrivait pas vraiment ce qu'on voulait ‐> tout était donc configuré bizarrement

Maintenant y'a un bug avec le gyro... j'essayais de mettre en place la lecture multiple la aussi...
Si on arrive pas a corriger on pourra toujours remettre l'ancienne versio

Avec le magnétomètre, la norme du vecteur vaut environ 0.5 gauss ce qui correcpond au champs magnétique terrestre donc ca doit être bon.

lundi 12 novembre 2012
12:49

A faire

lecture multiple i2c gyro échec implémentation balance filter ok

Constatation

La lecture multiple I2C du gyro impossible, retour à la version de Favre.

Implémentation du filtre complémentaire ok. Reste à modifier labview pour visualiser l'angle. sLettre K, 3 angles en float.

Il y a encore un problème avec le signal PWM, on constate une baisse de puissance d'environ 5% par intermittence. Certainement un problème de lecture, voir à l'oscillo pourquoi . Comme la retransmission du signal de la télécommande n'est pas une fonction finale, pas extrêment important de corriger ce bug.

Pour les portes‐ouvertes: flasher le programme dans la carte

dimanche 2 décembre 2012
11:16

A faire

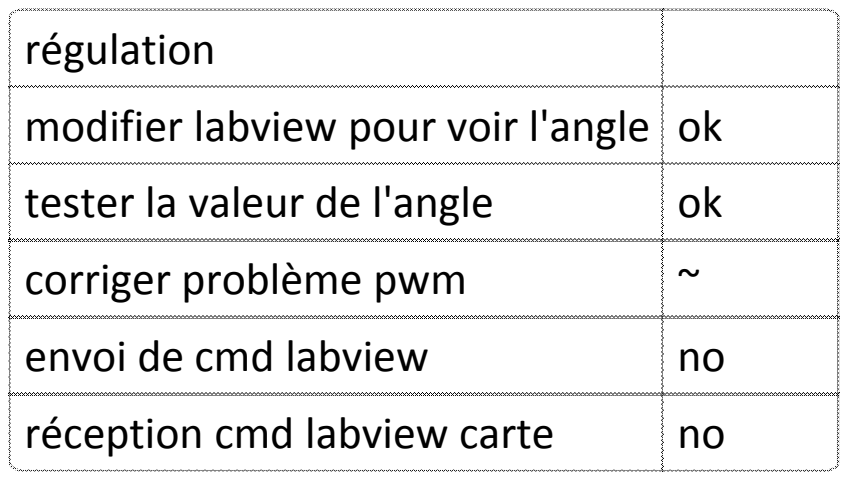
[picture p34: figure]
régulation; modifier labview pour voir l'angle ok; tester la valeur de l'angle; corriger problème pwm; envoi de cmd labview; réception cmd labview carte

Constatation

Il faut encore testé l'orientation du qadri avec un niveau pour voir si les valeurs sont précises. Mais à première vue les valeurs semble plausibles. On constate un léger bruit; éventuellement modifier le filtre pour le supprimer.

Le problème de stabilité du PWM ne vient pas d'une imprécision sur les floats.

lundi 3 décembre 2012
12:49

A faire

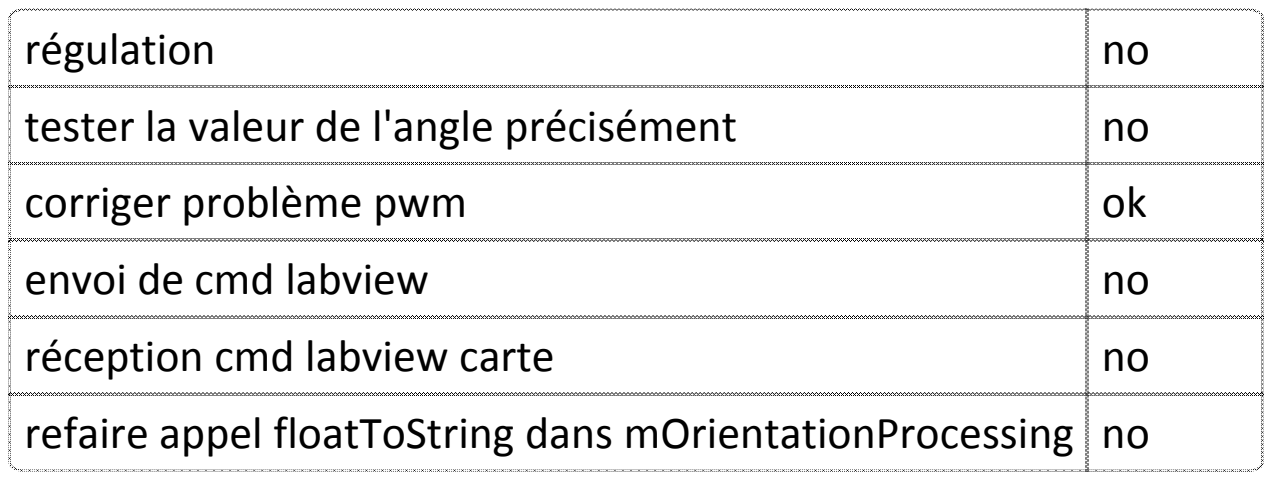
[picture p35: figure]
régulation; corriger problème pwm; envoi de cmd labview; réception cmd labview carte

tester la valeur de l'angle précisément | no

refaire appel floatToString dans mOrientationProcessing no

Constatation

Correction instabilité PWM. C'était un problème de lecture

lundi 10 décembre 2012
12:45

A faire

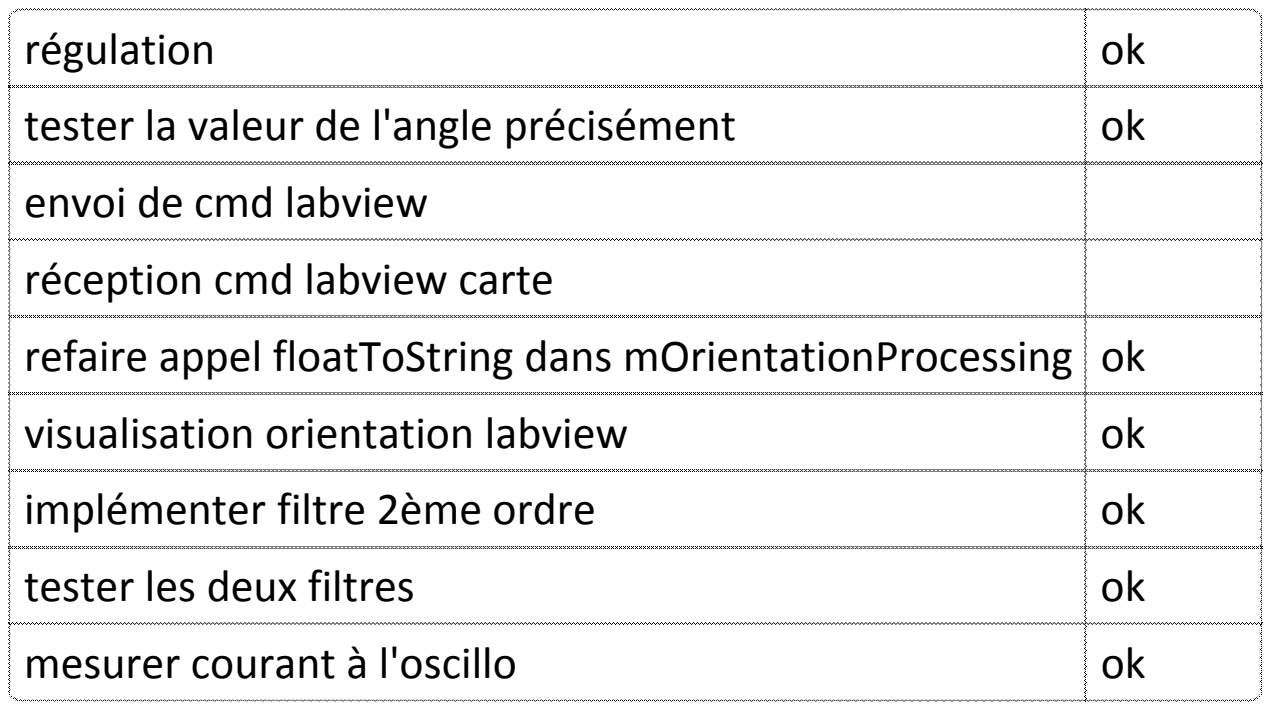
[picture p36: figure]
régulation; envoi de cmd labview; réception cmd labview carte; visualisation orientation labview; implémenter filtre 2ème ordre; tester les deux filtres; mesurer courant à l'oscillo

tester la valeur de l'angle précisément | ok

refaire appel floatToString dans mOrientationProcessing ok

Constatation

Le filtre du premier ordre comportait une faute.

Filtre du 2ème ordre implémenter, sélection du type de filtre dans la fonction execute.

Les angles d'orientation sont correct. Lorsque le quadricpotère est penché au maximum sur son support, on a 20° d'inclinaison dans labview. Une rapide mesure donne 17.5°

La mesure de courant labview est ok

Il y a une erreur avec un angle dans la reégul

La régulation est implémentée comme cela: tous les moteurs tourne à 50% de leur puissance et varie de +‐20%.

dimanche 6 janvier 2013
19:58

A faire

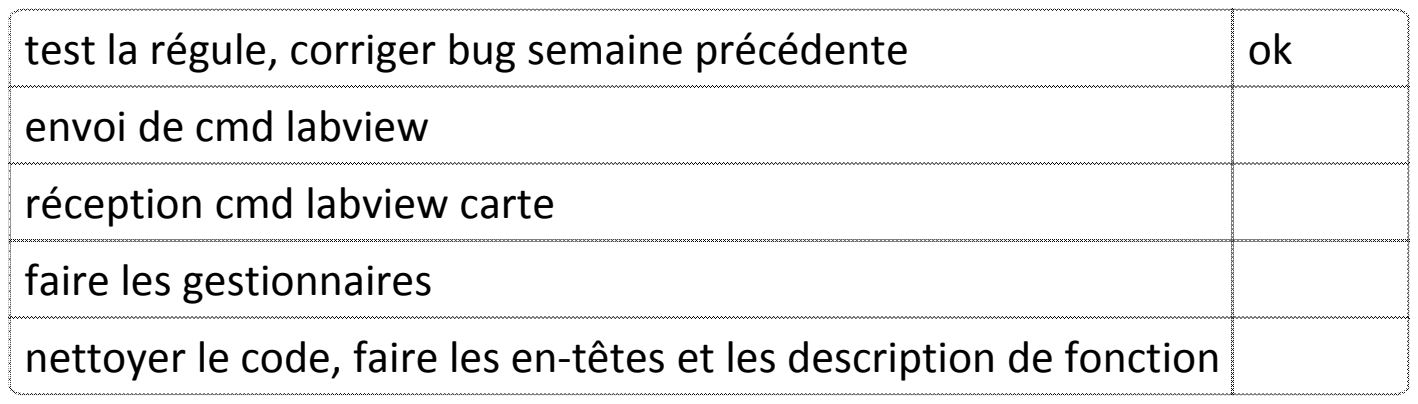
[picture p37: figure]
envoi de cmd labview; réception cmd labview carte; faire les gestionnaires

test la régule, corriger bug semaine précédente | ok

nettoyer le code, faire les en‐têtes et les description de fonction

Constatation

Essai régulateur P: modification duc oefficient de pondération de l'accelerometre à 0.4 dans le filtre
Implémetation régulateur I

Problème dans la fonction qui convertit les données de l'accel dans le système d'axe du gyro. Problème de réentrance avec la fonction de filtre 1er ordre

essai de la régule avec une puissance à 70%, pas encore suffisant pour décoller le quadri de la sphère. Les frottements empêche une régulation correcte à basse puissance

depuis que le filtre est corriger, nettement moins de bruit mais lent, pondération 40% accel

le régulateur I est pas fonctionnel, essai uniquement avec le régulateur P

lundi 7 janvier 2013
12:49

Après avoir visualiser le temps de cycle du main avec une led on c'est aperçu que c'est beaucoup trop lent.

Le coefficient a du filtre doit dépendre de Tao, ce n'était pas le cas.

La fréquence d'échantillonnage doit être 4‐5 fois plus grande que le Tao du filtre.

Le problème et que l'exécution de l'intteruption est trop lent pour q'elle soit exécutée toutes les 2ms, soit on a mal codé qqch soit le clock est mal réglé (peu probable)

tester vitesse clignotement led

lundi 21 janvier 2013
12:50

Faire un petit rapport, parler des correction de bug des intrefaces mais rapidement parler du hardware et de l'acquisition de l'orientation et de la régulation

détailler la trame pour le monitoring

séquence démarrage programme, arrêt d'urgence télécommande

## Documents

mercredi 23 janvier 2013
19:50

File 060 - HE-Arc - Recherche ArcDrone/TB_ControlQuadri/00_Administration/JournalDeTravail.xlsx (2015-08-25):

Journal de travail TB Electronique de commande d'un quadricoptère
Date | Tâche | Travail effectué | Début | Fin
2012-05-23
 | t1 | Recherche d'un régulateur de tension linéaire | 9:21:00 | 11:26:00
 | t2 | Recherche connecteurs driver moteurs | 11:26:00
 | t3 | Implantation capteur de pression | 13:00:00 | 15:00:00
 | t4 | Implantation capteur accel&magn | 15:30:00 | 18:20:00
2012-05-24
 | t1 | Implantation capteur accel&magn | 9:00:00 | 12:00:00
 | t2 | Implantation capteur gyroscope | 12:00:00 | 17:00:00
2012-05-25
 | t1 | Recherche module et kit de dévellopement maxstream | 9:45:00 | 16:30:00
2012-05-29
 | t1 | Placement des connecteurs sur la carte en collaboration avec le groupe de neuchatel | 13:00:00 | 16:00:00
2012-05-30
 | t1 | Implantation et footprint élément maxStream | 8:45:00 | 15:45:00
 | t2 | Test des signaux reçu par le récepteur | 9:45:00 | 10:15:00
2012-05-31
 | t1 | Révision globale du schéma électrique | 8:45:00 | 10:20:00
 | t2 | Implantation interface récepteur télécommande | 10:27:00 | 16:00:00
 | t3 | Implantation interface drivers moteurs | 16:00:00 | 17:30:00
2012-06-01
 | t1 | Implantation interface drivers moteurs | 9:00:00 | 10:45:00
 | t2 | Mesure de courant dimentionnement pour 50 A | 10:45:00 | 15:30:00
 | t3 | Apprentissage altium PCB | 15:30:00 | 16:15:00
2012-06-04
 | t1 | Implantation DC/DC | 8:45:00 | 11:35:00
 | t2 | Implantation interfaces cartes externes | 11:47:00 | 13:30:00
 | t3 | Révision du schéma avec Mr. Meyer | 13:30:00 | 15:00:00
 | t4 | Correction du schéma et mise à jour de la liste de composants | 15:30:00 | 17:30:00
2012-06-05
 | t1 | Finalisation du schéma électrique
2012-06-06
 | t1 | Finalisation du schémaélectrique
 | t2 | Commande des composants
2012-06-07
 | t1 | Réalisation PCB (Positionnement composants, définition rules, dimentionnement pcb) | 8:45:00 | 12:00:00
 | t2 | Réalisation PCB (interconnexion composants) | 13:00:00 | 16:00:00
2012-06-08
 | t1 | Réalisation PCB (interconnexion composants) | 8:45:00 | 16:00:00
2012-06-11
 | t1 | Réalisation PCB (interconnexion composants, finalisation) | 8:45:00 | 14:30:00
 | t2 | Test communication avec kit Xbee | 14:30:00 | 17:30:00
2012-06-12
 | t1 | Control footprints | 8:45:00 | 10:00:00
 | t2 | Administration | 10:00:00 | 10:30:00
 | t3 | Révision PCB (Connecteur debug) | 12:00:00 | 14:00:00
 | t4 | Installation outils de dévellopement | 14:00:00 | 17:30:00
2012-06-13
 | t1 | étude du code existant et du code restant à faire, lecture du datasheet | 9:45:00 | 17:30:00
2012-06-14
 | t1 | Lecture du datasheet, Etude du mapping et de l'initialisation de la cpu | 9:45:00 | 16:30:00
2012-06-15
 | t1 | Etude de l'evalKit KWIKSTIK, mise en œuvre des fonctions cpu, mapping, gpio | 8:45:00 | 16:30:00
2012-06-16
 | t1 | Etude des documents et rapports à rendre, planification | 14:00:00 | 16:30:00
2012-06-18
 | t1 | Mapping & clock | 8:45:00 | 18:00:00
 | t2 | Etude FlexTimer | 18:00:00 | 18:30:00
2012-06-19
 | t1 | Programmation Flextimer output compare | 8:45:00 | 17:30:00
2012-06-20
 | t1 | Programmation Flextimer Output compare | 8:45:00 | 17:30:00
2012-06-21
 | t1 | Programmation I2C | 8:45:00 | 17:30:00
2012-06-22
 | t1 | Programmation I2C | 8:45:00 | 14:00:00
 | t2 | Programmation Flextimer input capture | 14:00:00 | 16:30:00
2012-06-23
 | t1 | Programmation Flextimer input capture | 14:30:00 | 19:30:00
2012-06-25
 | t1 | Programmation Flextimer input capture | 8:30:00 | 21:30:00
2012-06-26
 | t1 | Programmation Uart Output | 8:30:00 | 18:30:00
2012-06-29
 | t1 | Montage Uc sur carte | 9:30:00 | 12:00:00
 | t2 | Programmation flextimer Output sur vraie carte | 12:00:00 | 20:00:00
2012-06-30
 | t1 | Programmation flextimer input sur carte | 14:00:00 | 19:30:00
2012-07-02
 | t1 | Résolution problèmes de clock, prog fletimer | 8:45:00 | 19:00:00
2012-07-03
 | t1 | Programmation interface RF (pour résoudre le FTM) | 7:30:00 | 15:30:00
 | t2 | Finalisation du FTM (input et output) | 15:30:00 | 20:30:00
 | t3 | Soudage plaque définitive
2012-07-04
 | t1 | Résolution problèmes de clock (plage de fréquence du quartz) | 8:45:00 | 19:30:00
2012-07-05
 | t1 | Résolution problème de clock (clock ok!) | 8:45:00 | 9:30:00
 | t2 | Programmation I2C | 9:30:00 | 17:30:00
 | t3 | Montage de l'alimentation, test (ne fonctionne pas) | 17:30:00 | 18:30:00
2012-07-06
 | t1 | Résolution problème alimentation (alimentation ok!) | 9:45:00 | 10:00:00
 | t2 | Prog interface module accelerometre magnetometre | 10:00:00 | 22:40:00
2012-07-07
 | t1 | Prog interface module gyroscope | 11:30:00 | 18:30:00
 | t2 | Debug magnétomètre (ko!) | 18:30:00 | 19:30:00
 | t3 | Etude spi | 19:30:00 | 21:30:00
2012-07-09
 | t1 | Programmation spi | 7:45:00 | 17:30:00
2012-07-10
 | t1 | Programmation spi (réussi) | 8:45:00 | 15:00:00
 | t2 | Prog mCapteur pression | 15:00:00 | 17:30:00
2012-07-11
 | t1 | Programmation AD | 8:45:00 | 13:15:00
 | t2 | Programmation mMesureAlimentation | 13:30:00 | 17:15:00
2012-07-12
 | t1 | Etude affichage données sur pc en C# | 8:45:00 | 16:00:00
2012-07-13
 | t1 | Compte rendu avec M. Meyer | 13:00:00 | 13:30:00

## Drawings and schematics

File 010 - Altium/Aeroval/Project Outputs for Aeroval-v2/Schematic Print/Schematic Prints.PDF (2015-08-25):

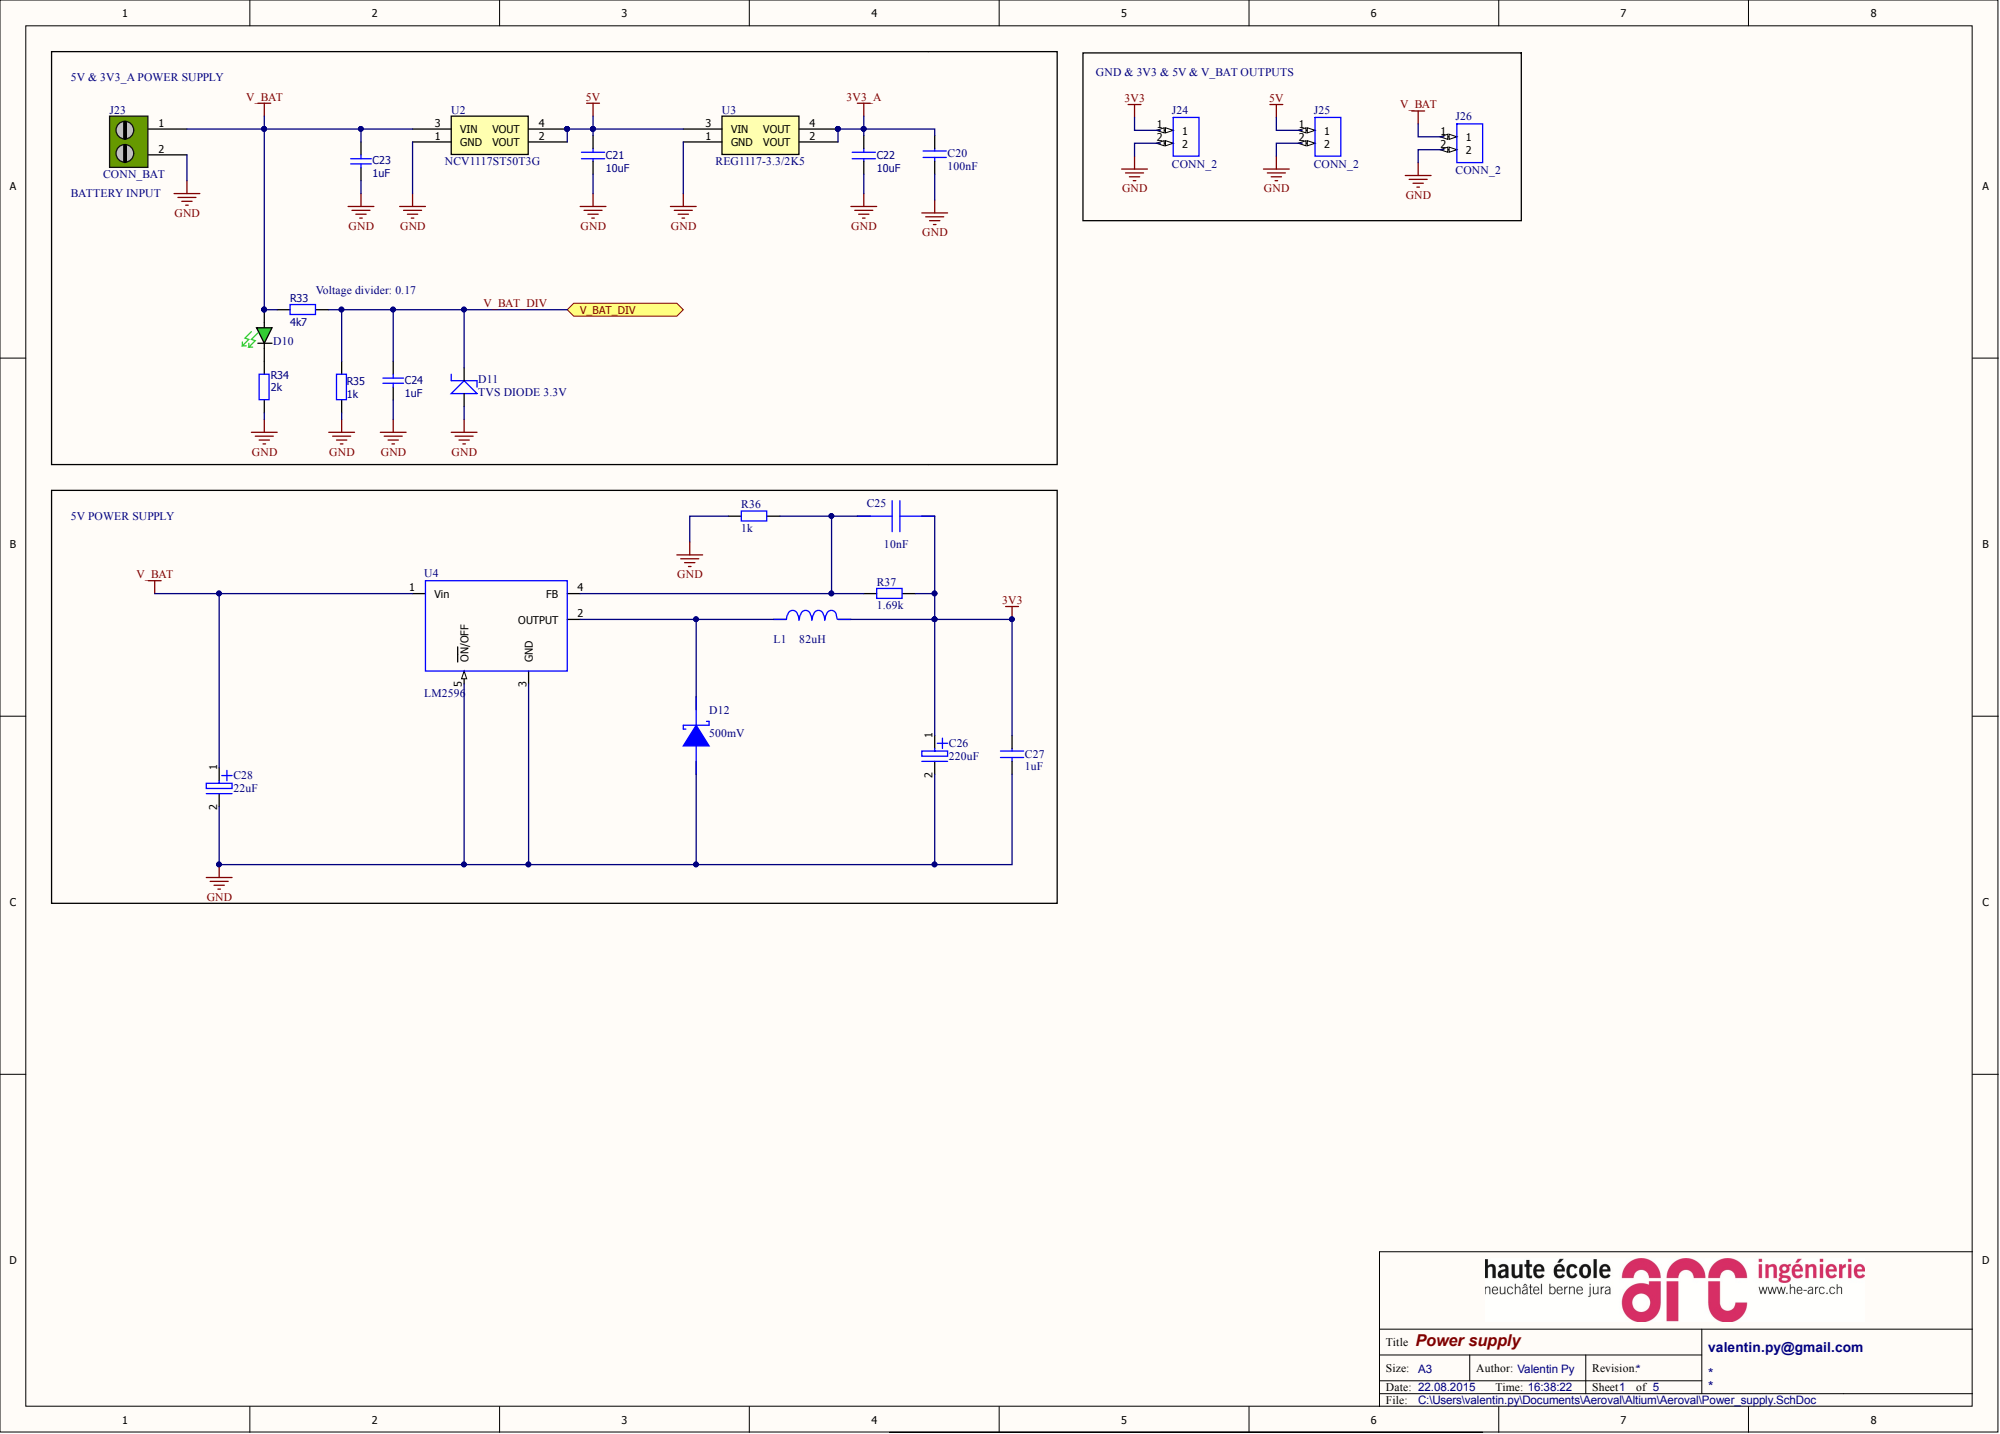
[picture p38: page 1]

valentin.py@gmail.com

Date:
C:\Users\valentin.py\Documents\Aeroval\Altium\Aeroval\Power_supply.SchDoc
File:

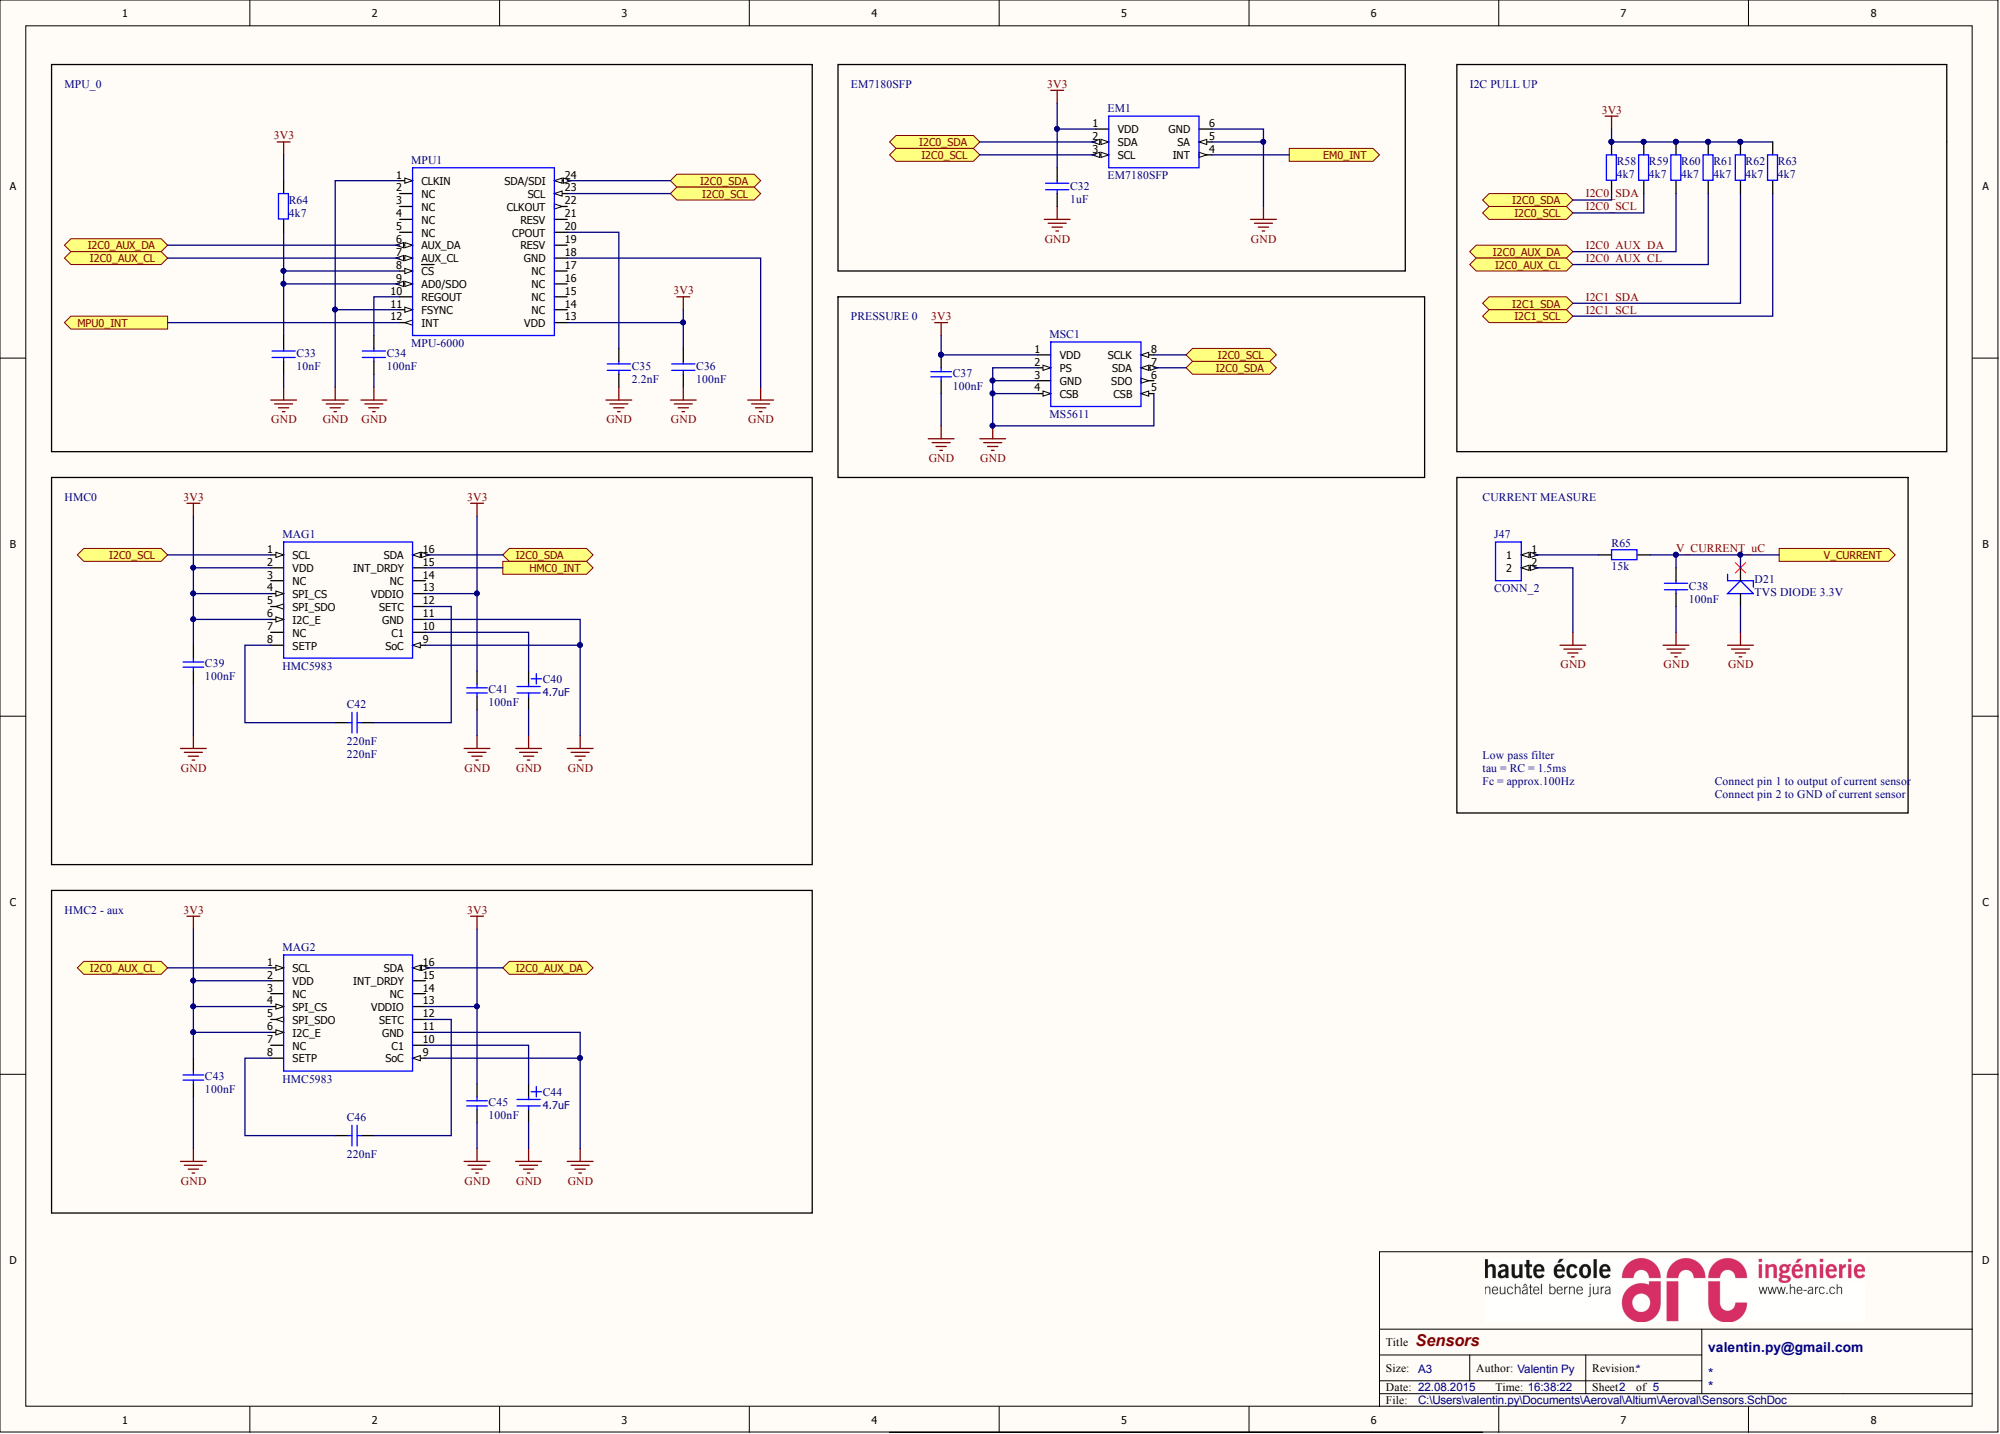
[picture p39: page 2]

AUX_DA 6 AUX_CL 7 CS 8

AD0/SDO 9
REGOUT 10

Connect pin 1 to output of current sensor
Connect pin 2 to GND of current sensor

C:\Users\valentin.py\Documents\Aeroval\Altium\Aeroval\Sensors.SchDoc

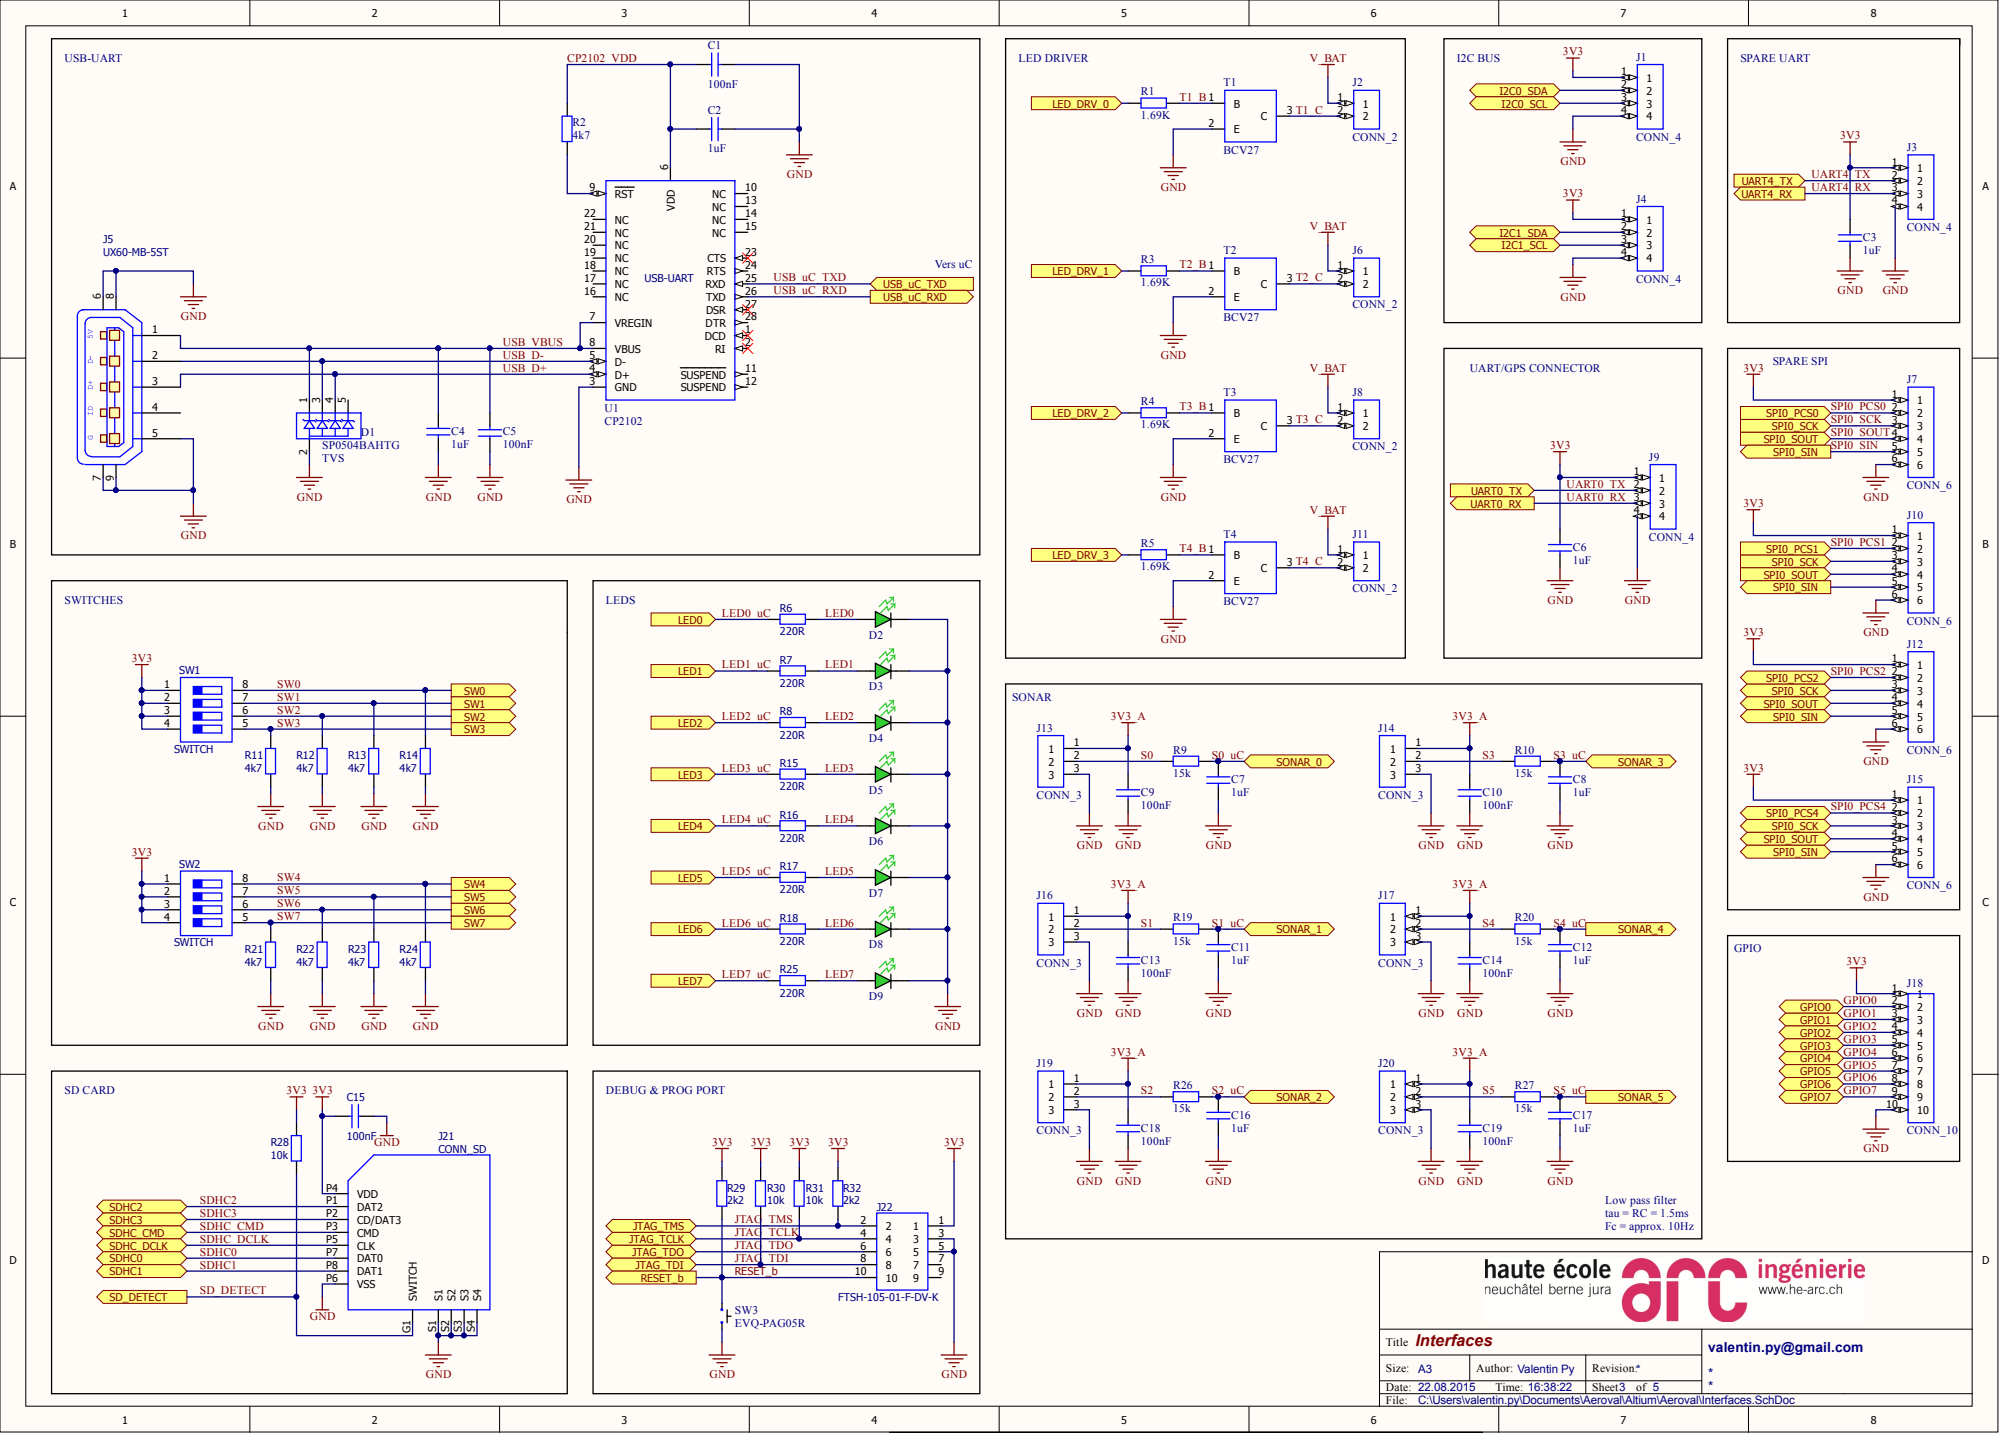
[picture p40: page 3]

USB_D+ | D+ 4

GND 3

2 | 7 SW1
3 | 6 SW2
4 | 5 SW3

3 | 6 SW6
4 | 5 SW7

C:\Users\valentin.py\Documents\Aeroval\Altium\Aeroval\Interfaces.SchDoc

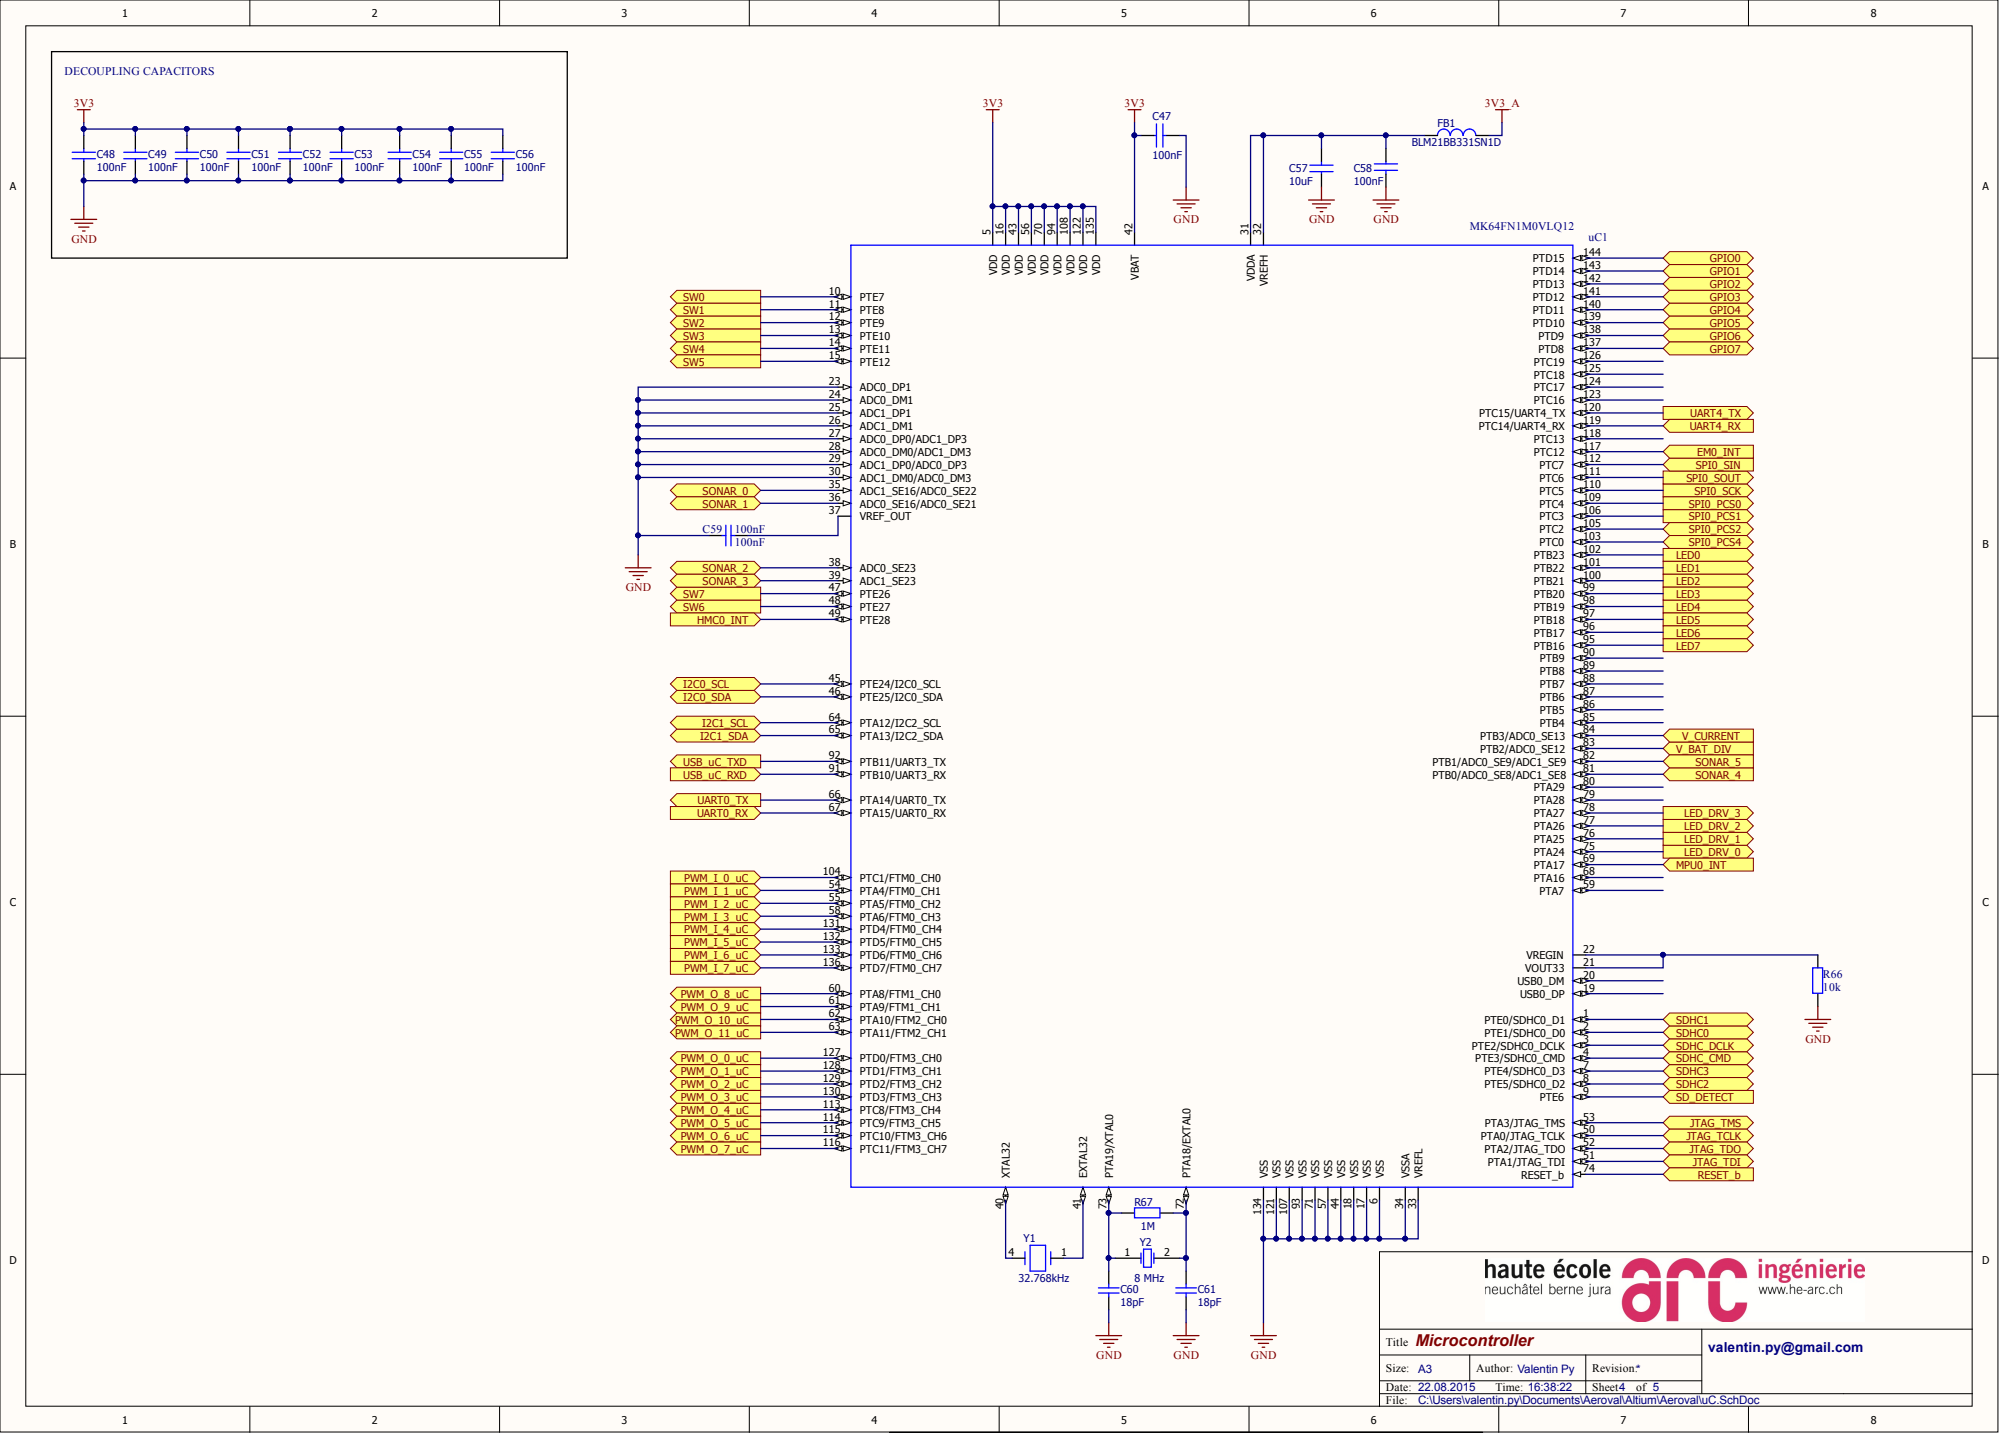
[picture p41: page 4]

C:\Users\valentin.py\Documents\Aeroval\Altium\Aeroval\uC.SchDoc

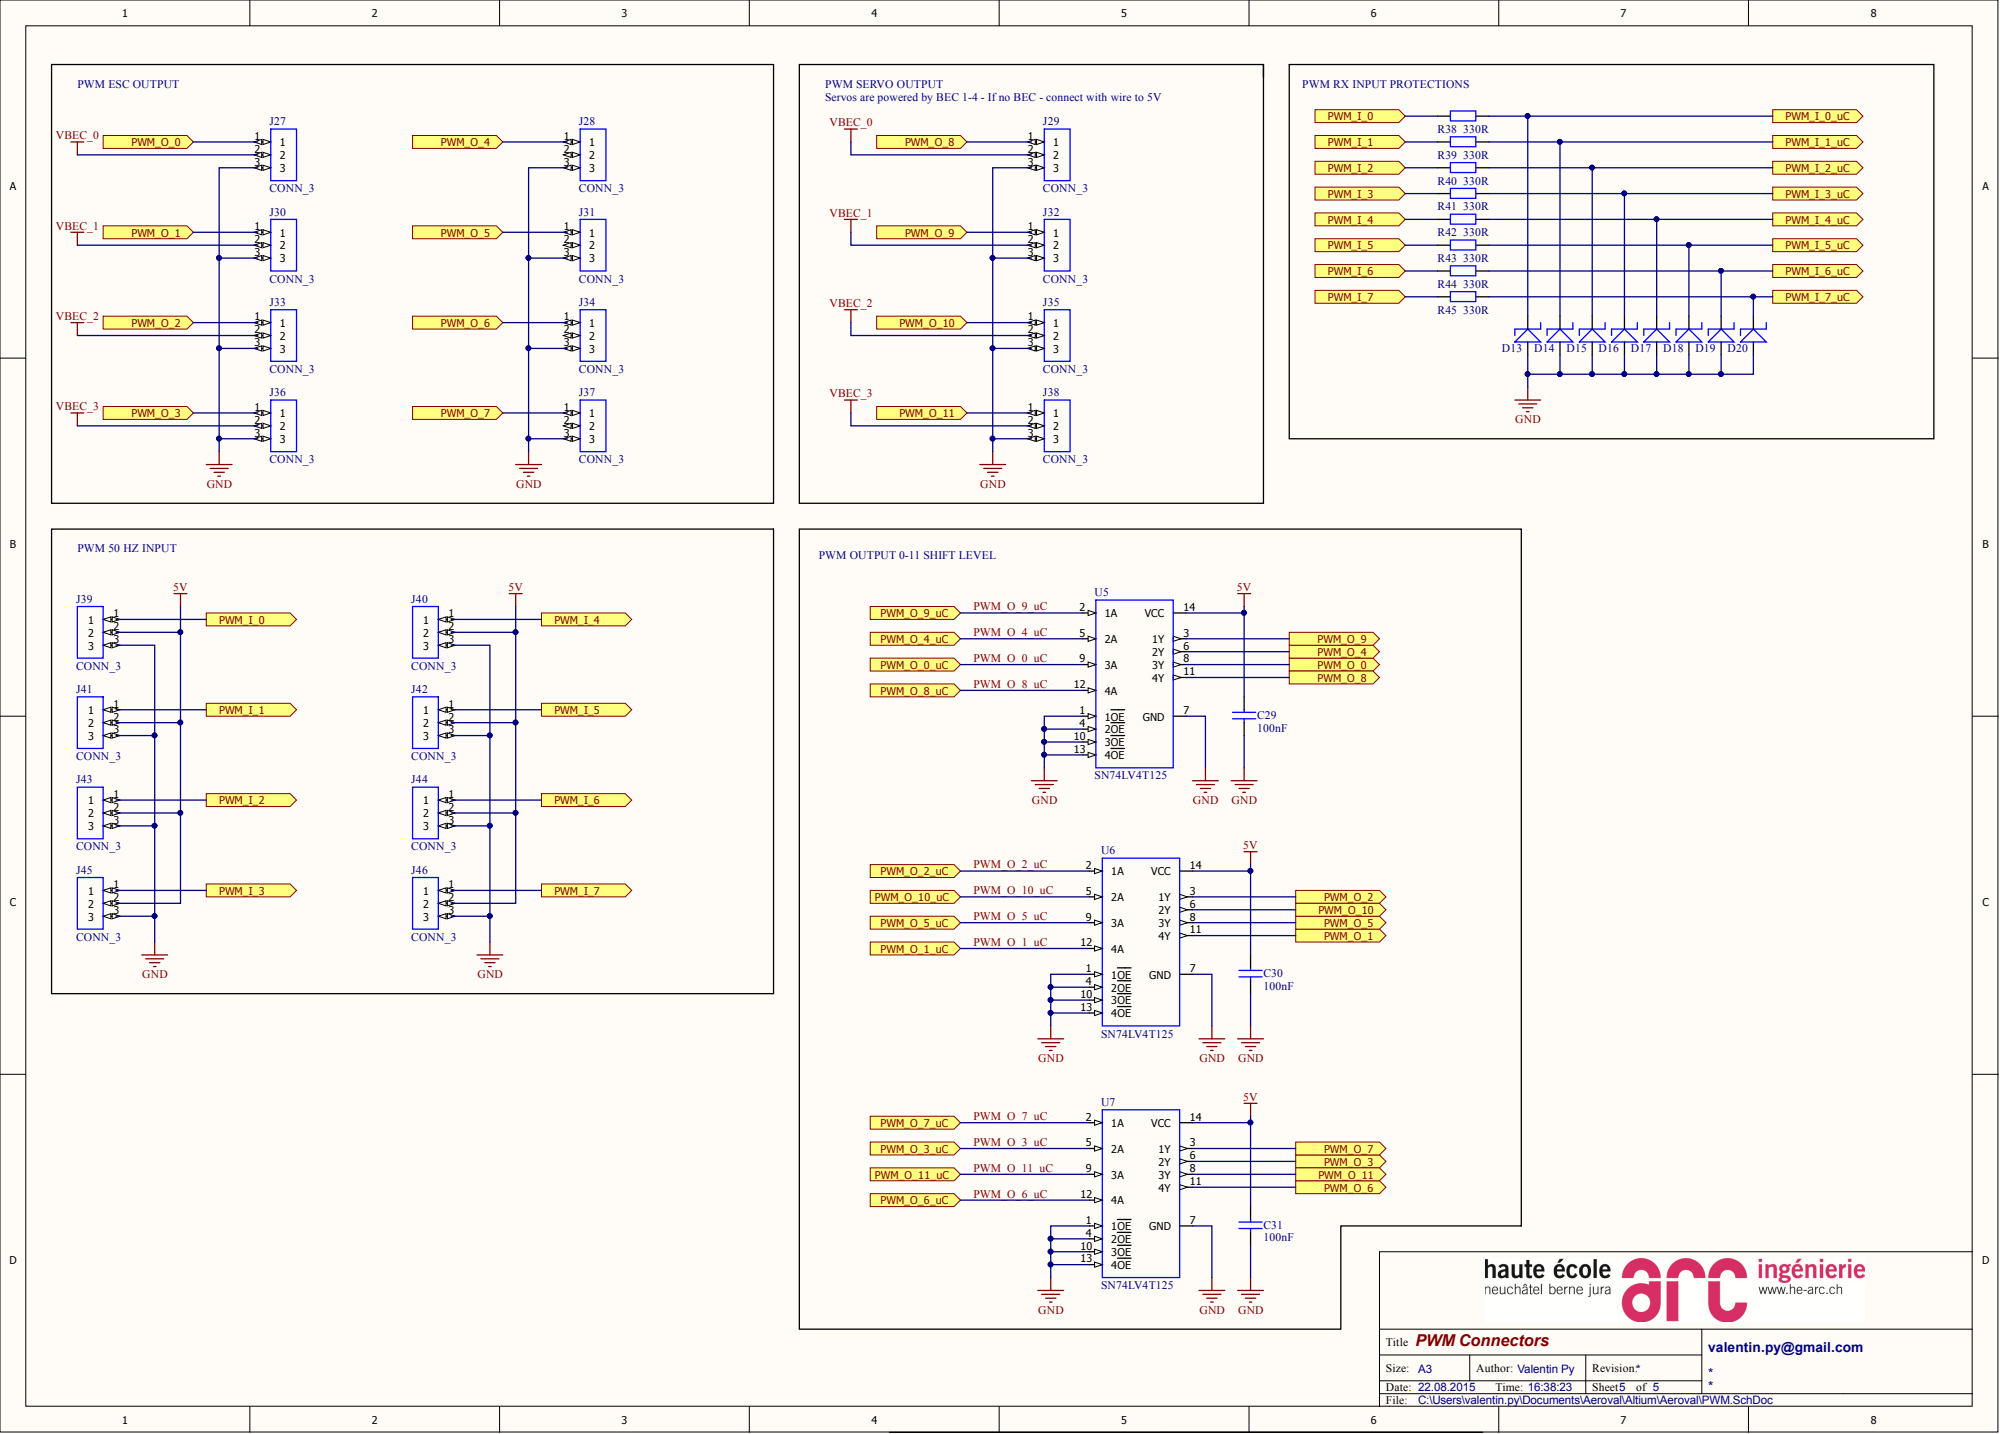
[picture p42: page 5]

PWM SERVO OUTPUT
Servos are powered by BEC 1-4 - If no BEC - connect with wire to 5V

PWM RX INPUT PROTECTIONS

PWM OUTPUT 0-11 SHIFT LEVEL

C:\Users\valentin.py\Documents\Aeroval\Altium\Aeroval\PWM.SchDoc

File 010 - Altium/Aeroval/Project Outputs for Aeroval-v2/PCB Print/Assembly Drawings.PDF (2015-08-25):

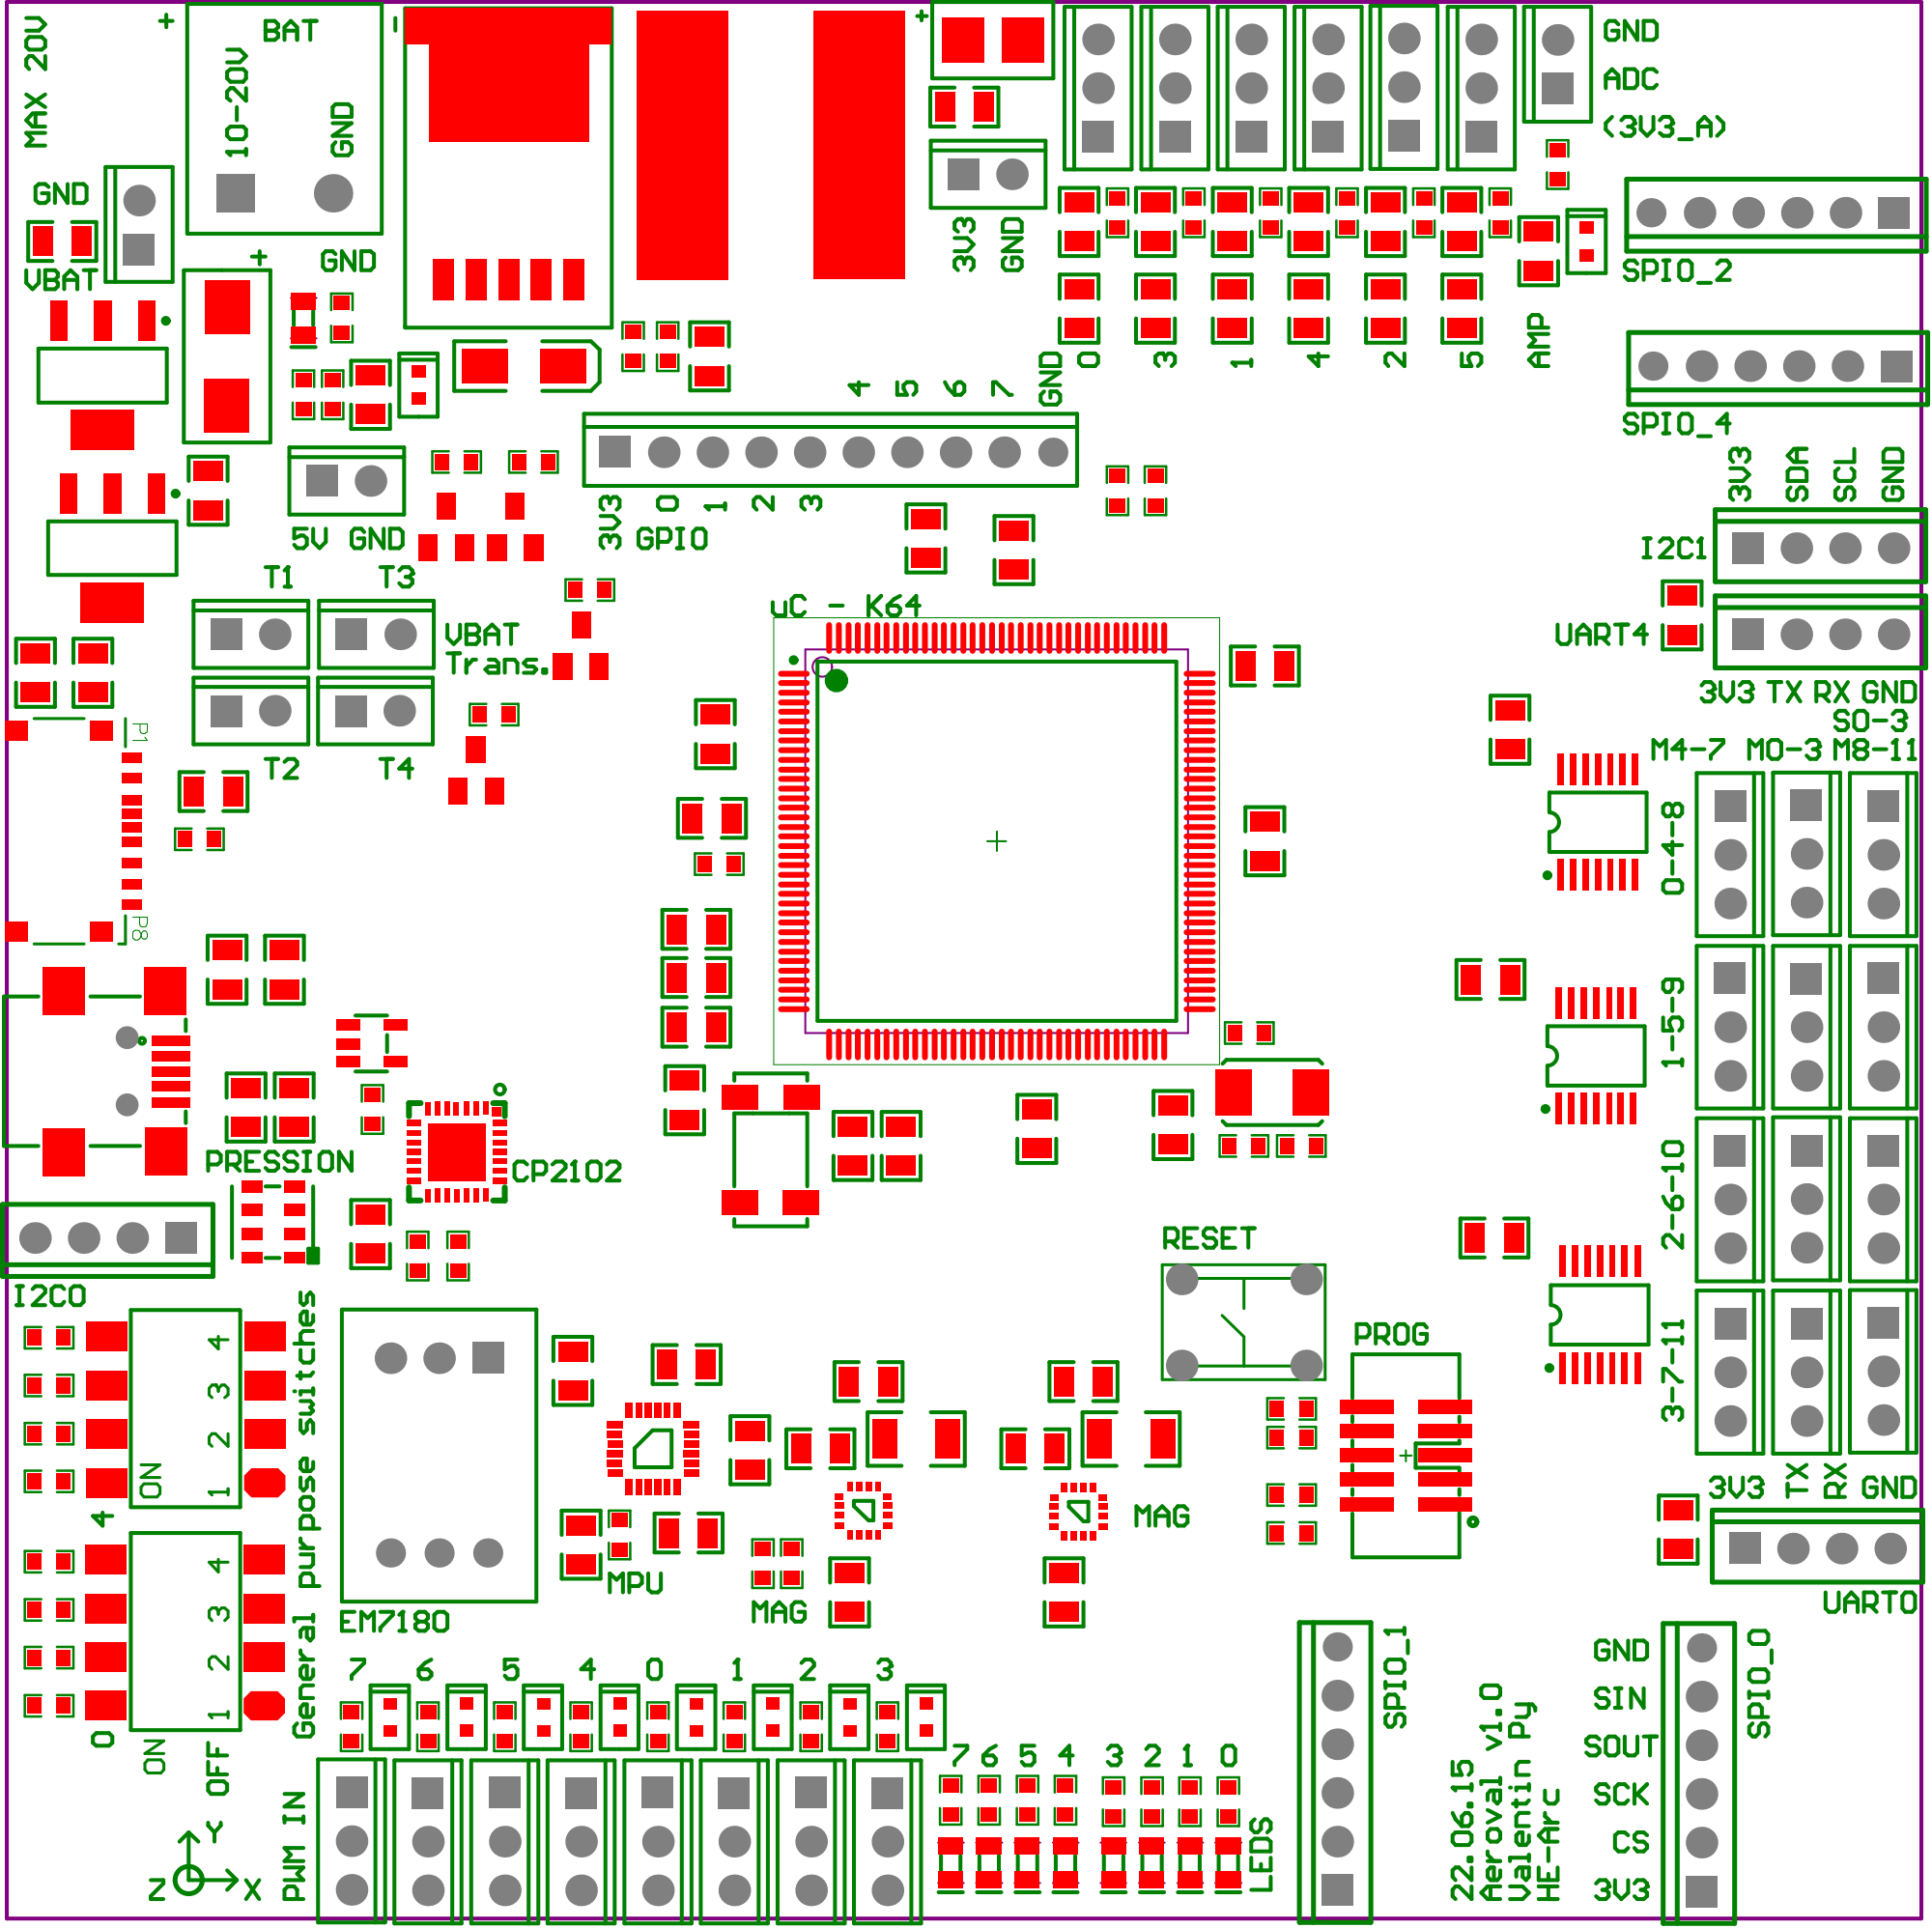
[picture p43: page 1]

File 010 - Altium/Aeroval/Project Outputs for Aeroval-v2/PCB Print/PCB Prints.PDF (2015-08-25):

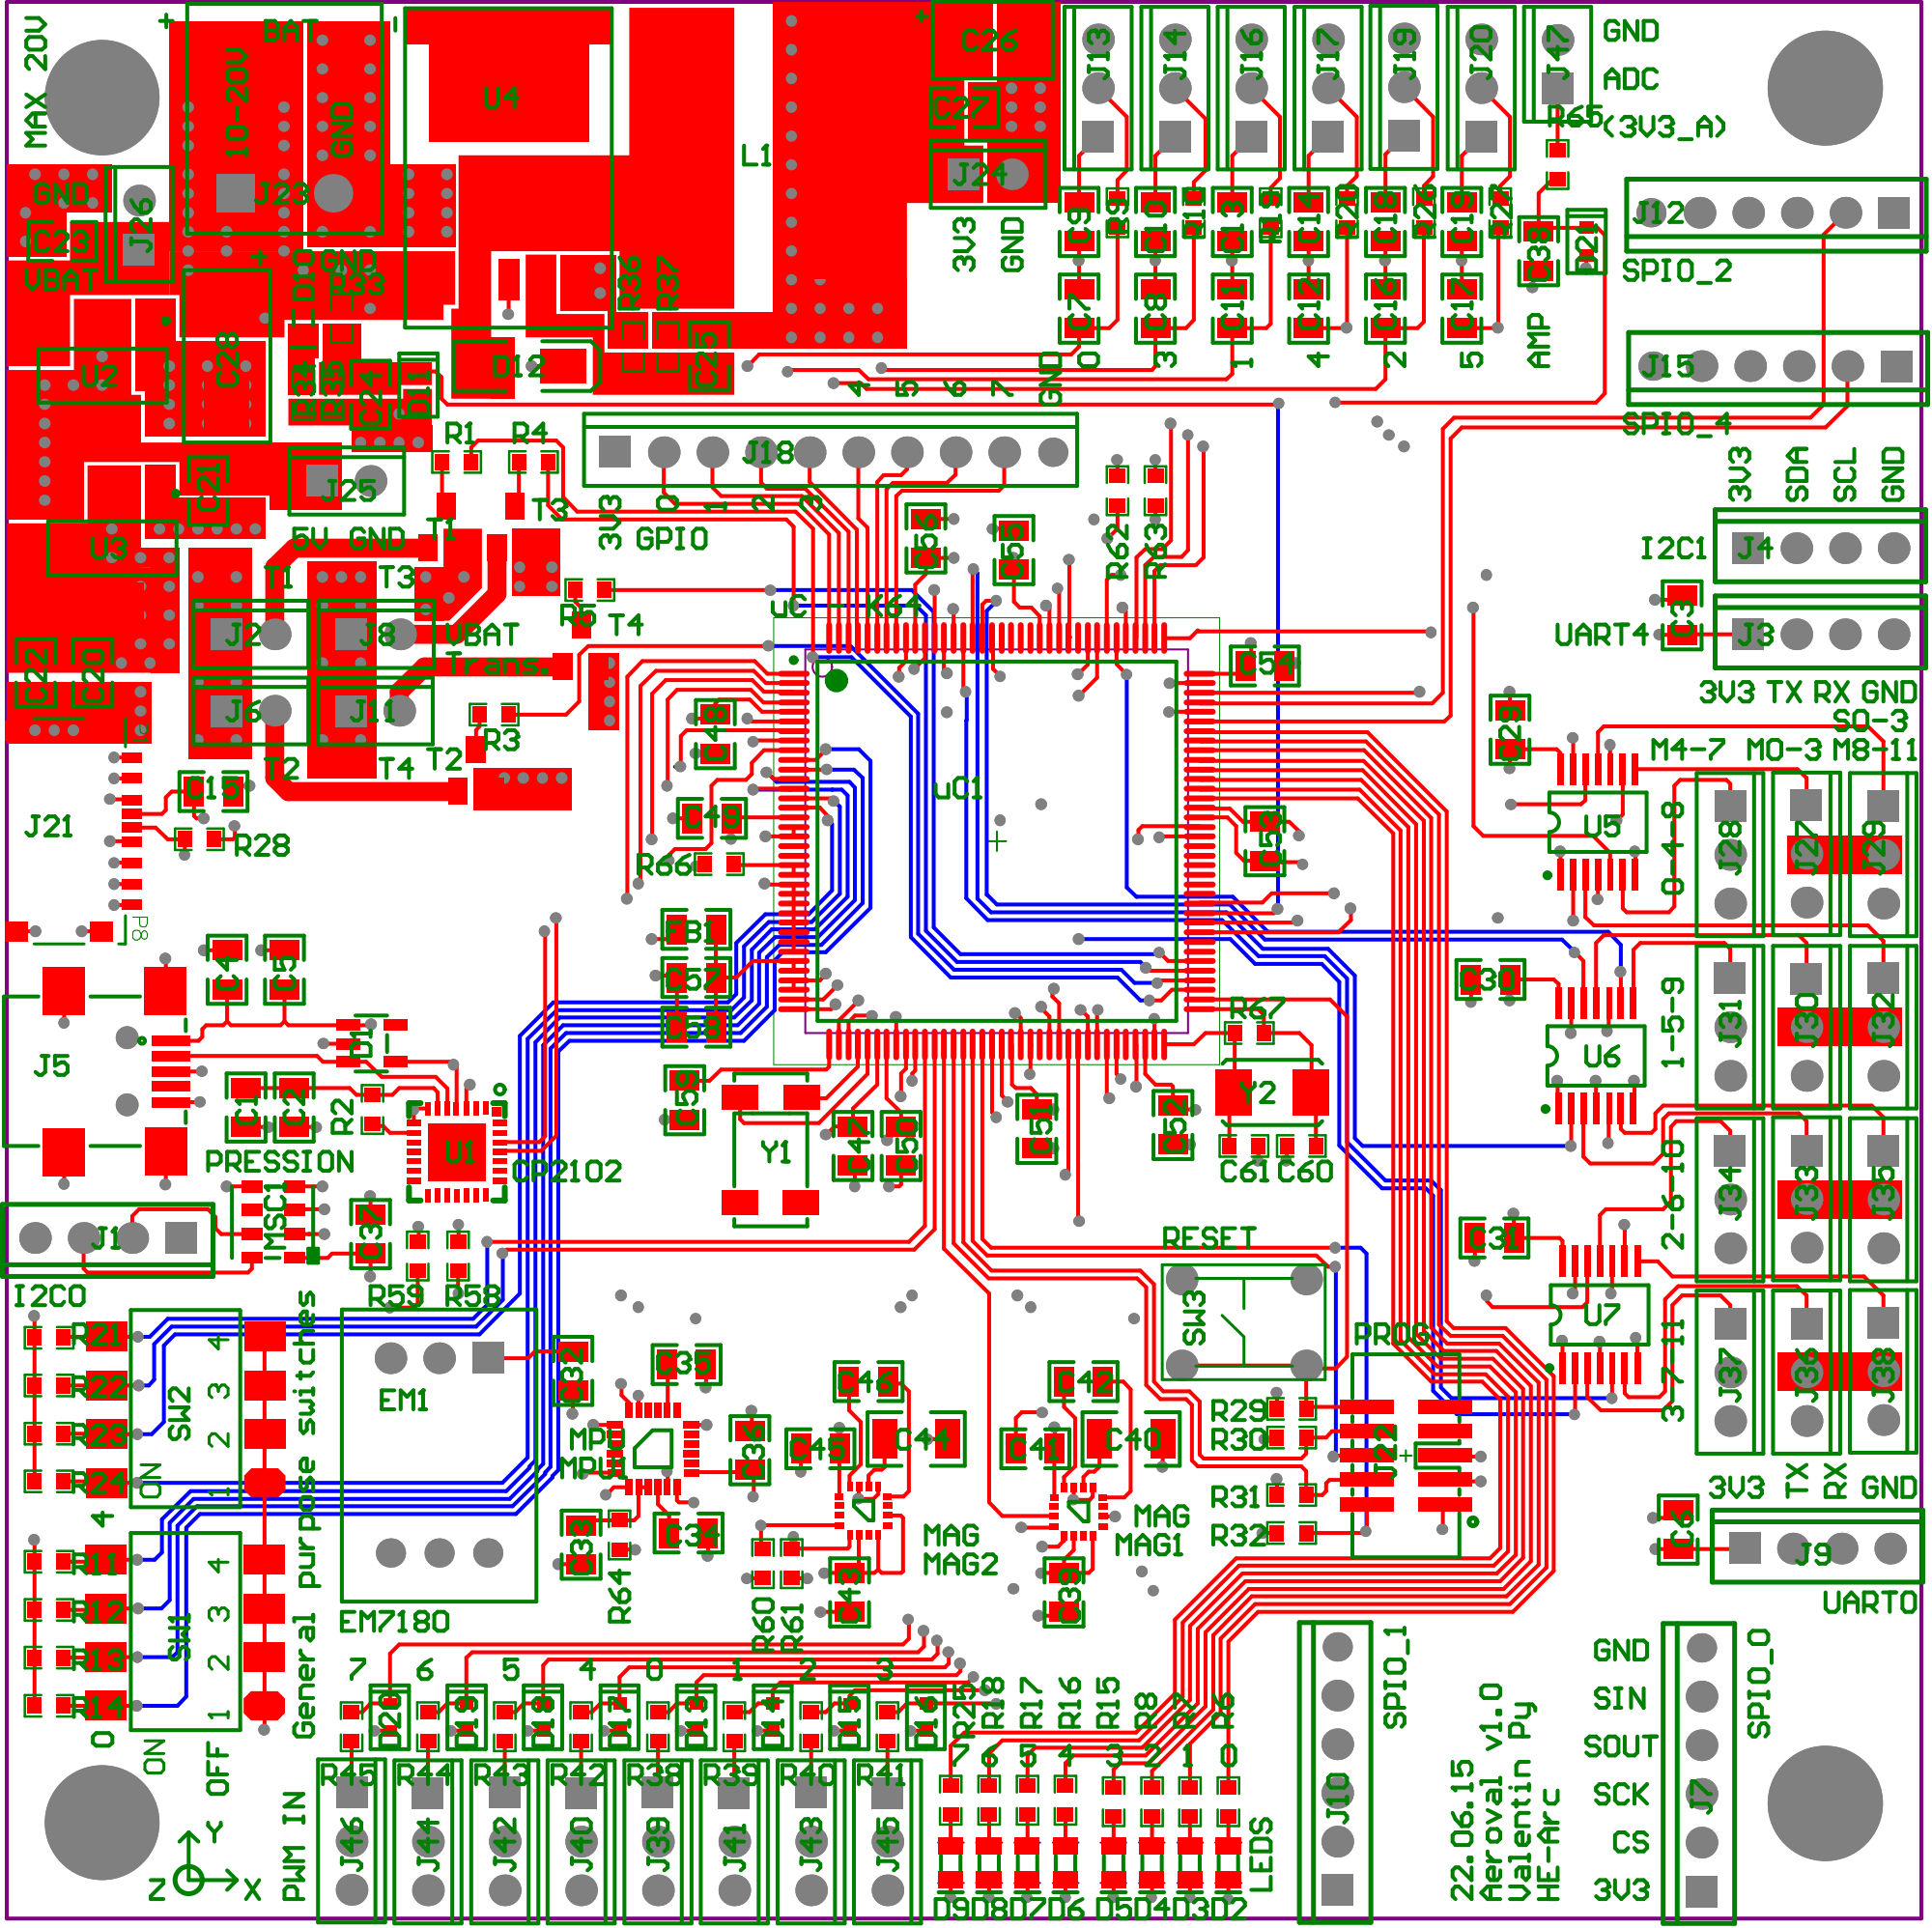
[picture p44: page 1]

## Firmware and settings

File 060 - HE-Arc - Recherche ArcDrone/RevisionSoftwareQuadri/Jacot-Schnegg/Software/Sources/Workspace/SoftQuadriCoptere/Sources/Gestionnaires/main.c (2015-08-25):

/*
------------------------------------------------------------
Copyright 2003-2013 Haute Ecole ARC Ingénierie,
Switzerland. All rights reserved
------------------------------------------------------------
Nom du fichier : 	main.c
Auteurs:			Alexandre Schnegg
					Guillaume Jacot
Date:				23.01.13
But :	Pilotage du quadricopère
------------------------------------------------------------
*/

#include <stdio.h>
#include <math.h>

#include "derivative.h" /* include peripheral declarations */
#include "mCpu.h"		/* PLL and crossbar configuration */
#include "mPwm.h"		/* FTMx configuration */
#include "mLeds.h"		/* Configuration Port leds */
#include "mRfInterface.h"
#include "mCapteurAccelMagn.h"
#include "mCapteurGyro.h"
#include "mCapteurPression.h"
#include "mMesureAlimentation.h"
#include "mOrientationProcessing.h"
#include "stringConvert.h"
#include "generateTrame.h"
#include "gMBox.h"
#include "gInput.h"
#include "gCompute.h"
#include "gOutput.h"
#include "iI2C.h"
#include "iCpu.h"
#include "iAd.h"
#include "iPit.h"
#include "iSpi.h"
#include "iUart.h"

void main(void)
{
	bool ledState = false;

	//-------------------------------------------------------------------------------
	// Setup des interfaces
	//-------------------------------------------------------------------------------
	iCpu_SysInit();
	iI2C_Setup();
	iUart_Config();
	iSpi_Setup();
	iPit_Config(kPit0, 2);
	iPit_StartPit(kPit0);
	iAd_Config();
	iAd_Cal(kAdc0);

	//-------------------------------------------------------------------------------
	// Open des interfaces
	//-------------------------------------------------------------------------------
	iI2C_Open();
	iUart_Open();
	iSpi_Open();

	//-------------------------------------------------------------------------------
	// Setup des modules
	//-------------------------------------------------------------------------------
	mCpu_Setup(); // PLL and crossbar configuration
	mLeds_Setup(); // Configuration Port leds
	mPwm_Setup(); // FTMx configuration
	mDelay_Setup();
	mRfInterface_Setup();
	mCapteurAccelMagn_Setup();
	mCapteurGyro_Setup();
	mCapteurPression_Setup();
	mMesureAlimentation_Setup();
	mOrientationProcessing_setup();

	mLeds_WriteLed(kLed2, kLedOn);

	//-------------------------------------------------------------------------------
	// Open des modules
	//-------------------------------------------------------------------------------
	mDelay_Open();
	mRfInterface_Open();
	mCapteurAccelMagn_Open();
	mCapteurPression_Open();

	mLeds_WriteLed(kLed3, kLedOn);

	//-------------------------------------------------------------------------------
	// Setup des gestionnaires
	//-------------------------------------------------------------------------------
	gInput_Setup();
	gCompute_Setup();
	gLabview_Setup();
	gOutput_Setup();

	mLeds_WriteLed(kLed4, kLedOn);
	
	mOrientationProcessing_open();		//A faire en dernier

	//-------------------------------------------------------------------------------
	// Execute des gestionnaires
	//-------------------------------------------------------------------------------
	while (1)
	{
		ledState = !ledState;
		mLeds_WriteLed(kLed5, ledState);

		gInput_Execute();
		gCompute_Execute();
		gLabview_Execute();
		gOutput_Execute();
	}
}

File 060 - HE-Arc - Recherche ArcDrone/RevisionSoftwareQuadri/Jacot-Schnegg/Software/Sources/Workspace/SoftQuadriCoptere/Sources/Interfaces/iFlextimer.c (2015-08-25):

/*
 ------------------------------------------------------------
 Copyright 2003-2012 Haute école ARC Ingéniérie, Switzerland. 
 All rights reserved.
 ------------------------------------------------------------
 File name :	iFlextimer.c
 Author and date :	Monnerat Serge 1 mars 2012

 Description in the header (.h)

 -----------------------------------------------------------------------------
 History:
 -----------------------------------------------------------------------------

 $History: $

 -----------------------------------------------------------------------------
 */

#include "iFlextimer.h"
#include "derivative.h"
#include "iDio.h"

#define FTM0_CLK_PRESCALE 4
#define FTM0_OVERFLOW_FREQUENCY (50)

#define FTM1_CLK_PRESCALE 4
#define FTM1_OVERFLOW_FREQUENCY (50)

#define FTM2_CLK_PRESCALE 1
#define FTM2_OVERFLOW_FREQUENCY (32768)

#define PERIPHERAL_BUS_CLOCK (50000000)

//Temps de latence entre le signal de chaques cannaux du récepteur de la télécommande (130us avec un échantillonage à 50MHz/4=12.5MHz --> 426 éch)
#define LATENCYECH 426

//mémorisation des mesures faites par Ftmx_CHn
static UInt16 sMesureFtm0_CH0_0 = 0;
static UInt16 sMesureFtm0_CH0_1_Temp = 0;
static UInt16 sMesureFtm0_CH0_1 = 0;
static UInt16 sMesureFtm0_CH1_0 = 0;
static UInt16 sMesureFtm0_CH1_1_Temp = 0;
static UInt16 sMesureFtm0_CH1_1 = 0;
static UInt16 sMesureFtm0_CH2_0 = 0;
static UInt16 sMesureFtm0_CH2_1_Temp = 0;
static UInt16 sMesureFtm0_CH2_1 = 0;
static UInt16 sMesureFtm0_CH3_0 = 0;
static UInt16 sMesureFtm0_CH3_1_Temp = 0;
static UInt16 sMesureFtm0_CH3_1 = 0;
static UInt16 sMesureFtm0_CH4_0 = 0;
static UInt16 sMesureFtm0_CH4_1 = 0;
static UInt16 sMesureFtm0_CH5_0 = 0;
static UInt16 sMesureFtm0_CH5_1 = 0;
static UInt16 sMesureFtm0_CH6_0 = 0;
static UInt16 sMesureFtm0_CH6_1 = 0;
static UInt16 sMesureFtm0_CH7_0 = 0;
static UInt16 sMesureFtm0_CH7_1 = 0;

//------------------------------------------------------------
// Flextimer setup
//------------------------------------------------------------
void iFlextimer_Config(void)
{
	static UInt32 aTmp = 0;

	//------------------------------------------------------------
	// FTM0
	//------------------------------------------------------------
	// Features Mode Selection (FTMx_MODE)
	// K10 Sub-Family Reference Manual, Rev. 6, Nov 2011 page 900
	// Disable Write Protection - enables changes to QUADEN, DECAPEN, etc.  
	FTM0_MODE |= FTM_MODE_WPDIS_MASK;
	//FTMEN is bit 0, need to set to zero so DECAPEN can be set to 0
	FTM0_MODE &= (~FTM_MODE_FTMEN_MASK);

	// Quadrature Decoder Control and Status (FTMx_QDCTRL)
	// K10 Sub-Family Reference Manual, Rev. 6, Nov 2011 page 923
	// Set Edge Aligned PWM
	FTM0_QDCTRL &= ~FTM_QDCTRL_QUADEN_MASK;

	// Counter (FTMx_CNT)
	// K10 Sub-Family Reference Manual, Rev. 6, Nov 2011 page 892
	// FTM Counter Value - reset counter to zero
	FTM0_CNT = 0x0; //FTM Counter Value - reset counter to zero

	// Modulo (FTMx_MOD)
	// K10 Sub-Family Reference Manual, Rev. 6, Nov 2011 page 892
	//Set the overflow rate
	FTM0_MOD = (PERIPHERAL_BUS_CLOCK / (1 << FTM0_CLK_PRESCALE)) / FTM0_OVERFLOW_FREQUENCY;

	// Counter Initial Value (FTMx_CNTIN)
	// K10 Sub-Family Reference Manual, Rev. 6, Nov 2011 page 897
	//Set the Counter Initial Value to 0
	FTM0_CNTIN = 0;

	// Channel (n) Status and Control (FTMx_CSC)
	// K10 Sub-Family Reference Manual, Rev. 6, Nov 2011 page 893
	// CHIE=0, Disable channel interrupts. Use software polling
	// MSB/MSA/ELSB/ELSA --> Edge-aligned PWM
	// DMA=0, Disable DMA transfers
	//Channel 0 Input capture
	FTM0_C0SC = 0;
	FTM0_C0SC |= FTM_CnSC_CHIE_MASK | FTM_CnSC_ELSB_MASK | FTM_CnSC_ELSA_MASK;//Interrupt enable
	//Channel 1 Input capture
	FTM0_C1SC = 0;
	FTM0_C1SC |= FTM_CnSC_CHIE_MASK | FTM_CnSC_ELSA_MASK | FTM_CnSC_ELSB_MASK;
	//Channel 2 Input capture
	FTM0_C2SC = 0;
	FTM0_C2SC |= FTM_CnSC_CHIE_MASK | FTM_CnSC_ELSA_MASK | FTM_CnSC_ELSB_MASK;
	//Channel 3 Input capture
	FTM0_C3SC = 0;
	FTM0_C3SC |= FTM_CnSC_CHIE_MASK | FTM_CnSC_ELSA_MASK | FTM_CnSC_ELSB_MASK;
	//Channel 4 Output compare
	FTM0_C4SC = 0;
	FTM0_C4SC |= (FTM_CnSC_MSB_MASK | FTM_CnSC_ELSB_MASK);
	//Channel 5 Output compare
	FTM0_C5SC = 0;
	FTM0_C5SC |= (FTM_CnSC_MSB_MASK | FTM_CnSC_ELSB_MASK);
	//Channel 6 Output compare
	FTM0_C6SC = 0;
	FTM0_C6SC |= (FTM_CnSC_MSB_MASK | FTM_CnSC_ELSB_MASK);
	//Channel 7 Output compare
	FTM0_C7SC = 0;
	FTM0_C7SC |= (FTM_CnSC_MSB_MASK | FTM_CnSC_ELSB_MASK);

	//Config de l'interruption
	// IRQ bit offset in the following registers
	aTmp = 62 % 32;
	// DUI0553A_cortex_m4_dgug.pdf page page 222 
	// Interrupt Clear-pending Registers
	// Clear prending interrupt
	NVICICPR1 |= (1 << aTmp);
	// DUI0553A_cortex_m4_dgug.pdf page page 220
	// Interrupt Set-enable Registers
	// Interrupt enable
	NVICISER1 |= (1 << aTmp);
	// DUI0553A_cortex_m4_dgug.pdf page page 223
	// Interrupt Priority Registers
	// Set interrupt priority
	NVICIP62 = kFTM0_IntPriority;

	// Status and Control (FTMx_SC)
	// K10 Sub-Family Reference Manual, Rev. 6, Nov 2011 page 890
	// Edit registers when no clock is fed to timer so the MOD value, gets pushed in immediately
	FTM0_SC = 0;

	// Channel (n) Value (FTMx_CV)
	// K10 Sub-Family Reference Manual, Rev. 6, Nov 2011 page 896
	// FTMx_CnV contains the captured FTM counter value, this value determines the pulse width
	// Duty at 50%
	FTM0_C0V = 0.5 * FTM0_MOD;
	FTM0_C1V = 0.5 * FTM0_MOD;
	FTM0_C2V = 0.5 * FTM0_MOD;
	FTM0_C3V = 0.5 * FTM0_MOD;
	FTM0_C4V = 0.5 * FTM0_MOD;
	FTM0_C5V = 0.5 * FTM0_MOD;
	FTM0_C6V = 0.5 * FTM0_MOD;
	FTM0_C7V = 0.5 * FTM0_MOD;

	// Status and Control (FTMx_SC)
	// K10 Sub-Family Reference Manual, Rev. 6, Nov 2011 page 890
	// CPWMS=0,Center-aligned PWM Select -> FTM counter operates in up counting mode
	// CLKS=1, Clock Source Selection -> System clock -> 50Mhz
	// PS:3,Prescale Factor Selection -> Divide by 8 
	FTM0_SC |= (FTM_SC_CLKS(1) | FTM_SC_PS(FTM0_CLK_PRESCALE));

	// FTM PWM Load (FTMx_PWMLOAD)
	// K10 Sub-Family Reference Manual, Rev. 6, Nov 2011 page 933
	FTM0_PWMLOAD |= FTM_PWMLOAD_LDOK_MASK;

	//------------------------------------------------------------
	// FTM1
	//------------------------------------------------------------
	// Features Mode Selection (FTMx_MODE)
	// K10 Sub-Family Reference Manual, Rev. 6, Nov 2011 page 900
	// Disable Write Protection - enables changes to QUADEN, DECAPEN, etc.  
	FTM1_MODE |= FTM_MODE_WPDIS_MASK;
	//FTMEN is bit 0, need to set to zero so DECAPEN can be set to 0
	FTM1_MODE &= (~FTM_MODE_FTMEN_MASK);

	// Quadrature Decoder Control and Status (FTMx_QDCTRL)
	// K10 Sub-Family Reference Manual, Rev. 6, Nov 2011 page 923
	// Set Edge Aligned PWM
	FTM1_QDCTRL &= ~FTM_QDCTRL_QUADEN_MASK;

	// Counter (FTMx_CNT)
	// K10 Sub-Family Reference Manual, Rev. 6, Nov 2011 page 892
	// FTM Counter Value - reset counter to zero
	FTM1_CNT = 0x0; //FTM Counter Value - reset counter to zero
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
